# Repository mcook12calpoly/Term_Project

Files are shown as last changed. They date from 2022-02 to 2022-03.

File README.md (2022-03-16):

# Term Project - Plotting Machine

For this term project, a 2.5 axis plotting machine was contructed using a pivoting arm driven by a motor attached to a wheel at the end of the arm. Alongside the arm, a lead screw driven by a second motor which will move a pen carrier linearly along the arm. Within the pen carrier is a servo attached to the pen to raise and lower the pen. A small piece wraps around tip of the pen to allow the servo arm to push it upwards. The body of the arm and the base is made of square metal tubing and the pen chassis as well as the coupling piece that connects the arm and carrier to keep the pen carrier upright will be 3D printed. The pivoting mechanism includes a bearing to minimize slop in our rotation. Limit switches are used to signal when the arm is in its home position. The encoders included with the motors are used to track the movement of the arm and determine the pen's location. The code uses kinematic calculations to convert the x,y plot directions to the curvilinear movement of the arm and pen carrier.

---

### Bill of Materials

| Qty. | Part | Source | Est. Cost |
|:----:|:---|:---|:---:|
|  2 | Pittman Gearmotors | ME405 Tub | - |
|  1 | Nucleo with Shoe | ME405 Tub | - |
|  1 | Nucleo Motor Driver | ME405 Tub | - |
|  5 | Hobby Micro Servo | Amazon&trade; | $8.99 |
|  1 | 400mm Lead Screw | Amazon&trade; | $12.99  |
|  1 | 96" Square Metal Tube | Home Depot&trade; | $22.26  |
|  1 | Triplus Fineliner Pen | Already Owned | $1.29 |
|  1 | Chassis for servo/pen | 3D Printer | - |
|  1 | Limit Switch | Already Owned | - |
|  2 | Wheel | 3D Printer | - |

---
### Hardware Design
The frame for our machine was constructed of aluminum tubing and 3d printed connectors. The central connector had mounting points for the pivot arm's limit switch as well as the hinge for the pivot arm. The pivot arm was also constructed out of alumininum tubing with a 3d printed motor mount and coupler at the end that attached to a 3d printed wheel with rubber bands for grip. Opposite the wheel on the arm is another 3d printed motor mount and coupler that operated the lead screw which is supported by a bearing on the other end placed within the wheel motor's mount. The pen holder was also 3d printed and made to wrap around the pivot arm and move with the lead screw by attaching to the copper nut provided with the lead screw. 

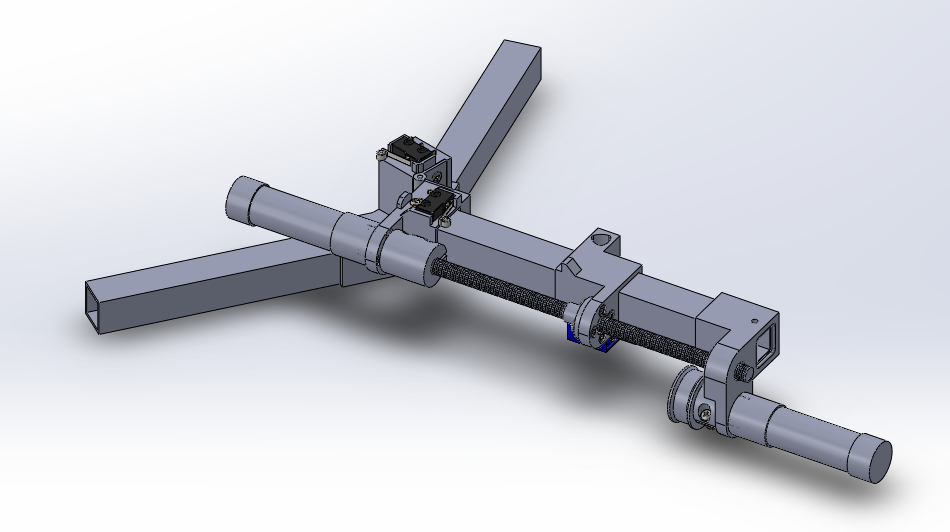
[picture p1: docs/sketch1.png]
projectsketch1

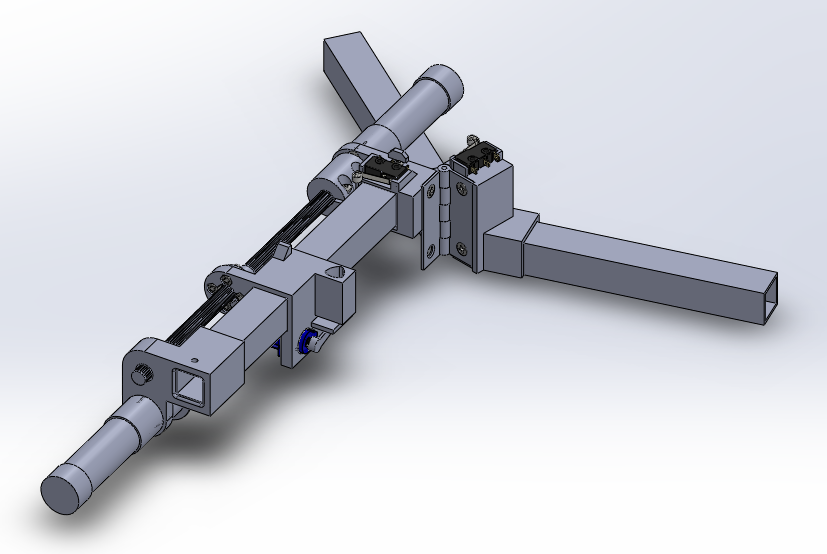
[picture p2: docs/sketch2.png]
projectsketch2

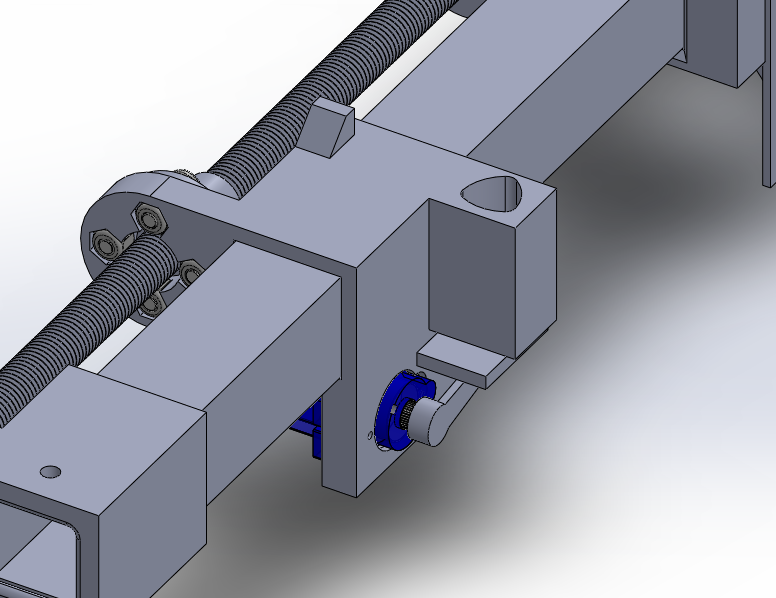
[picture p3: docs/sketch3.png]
projectsketch3


---
### Software Design
The software begins with a custom GCode file that is processed through a script that goes line by line and convcerts each command into polar setpoints of r and theta and a pen state(up or down). This processed list of setpoints is then loaded on the board where it can be read by the main file, with each line placed in a queue. After initially sending both motors (screw and wheel) back to their home positions near the origin, three tasks are created and added to the task list: update encoder, move and read. The update encoder task updates the encoder drivers to get the current position values for both motors, the move task moves the motors (and pen servo if applicable) until their corresponding enocders reach the current setpoint on the top of the queue. The read task adds each line of setpoints to the queue one at a time.

Link to Doxygen: https://mcook12calpoly.github.io/Term_Project/

---
### Results
After some initial testing and reworking of our software, the first successful drawing was of a rectangle. Due to the changes made on how the Gcode processing script determines the resolution of each line drawn, we were able to get much better looking and consistent long lines. The lines of the rectangle did not display any large zigzags as our device had been producing before the changes. However, the lines were not perfectly aligned and created angles that were not 90 degrees in the rectangle. We believe that this issue was due to the home position of our pen holder relative to the expected origin of our axis.

---
### Lessons Learned
The combination of 3d printed parts and aluminum tubing for the frame of the machine made the construction very durable for our testing uses and allowed the mechanical side of the machine to run without issue, leaving more time to focus on software.

We did not initially think to factor in the distance between the pivot(hinge) and the resting home position of the pen in its holder. This would have given us an offset radial value for what should be home or (0,0). This is likely why our rectange did not have straight angles in our testing. In addition, we learned quite a bit about task timing and efficiency. Reducing the period of certain tasks such as our move task and read task greatly improved the resolution of our machine, as it took less time for the next setpoint to be ready. 

If we were to write the code for this machine again, one improvement that we would make would be to implement Bresenham's line drawing algorithm, which would better help us calculate setpoints so that the steps in straight lines are less noticable. In addition to this, we would parse the setpoints and load them into memory before the machine runs, instead of parsing the setpoints each time the read task is called. This would likely improve the performance of our program, allowing us to run at finer setpoint resolutions. Although we didn't experience any issues with sensor resolution, their effect(especially on the wheel) could be noticable with better code performance. A potentiometer could be implemented on the pivot of the arms, which would allow for better accuracy and negate any error from wheel slippage. Also, the implementation of a PID controller could help with line smoothness due to the acceleration and decelleration of both axis.

---

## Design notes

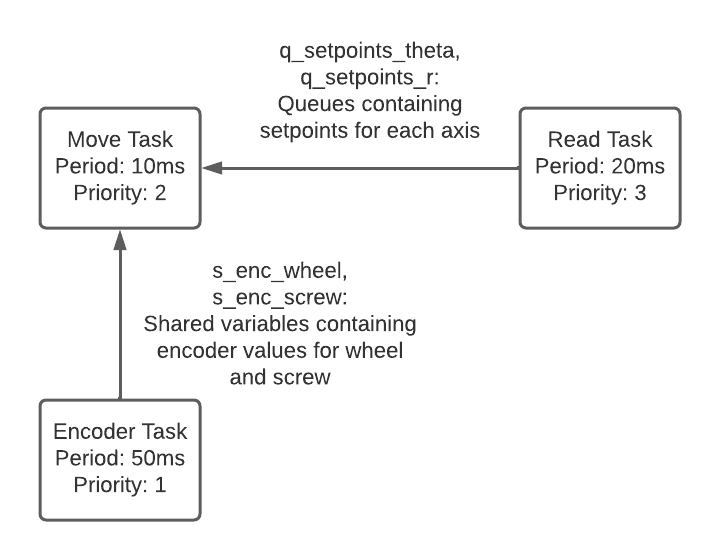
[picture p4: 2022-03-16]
docs/Task_Diagram.png

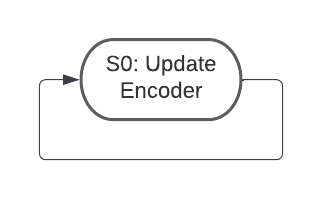
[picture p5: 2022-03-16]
docs/Encoder_FSM.png

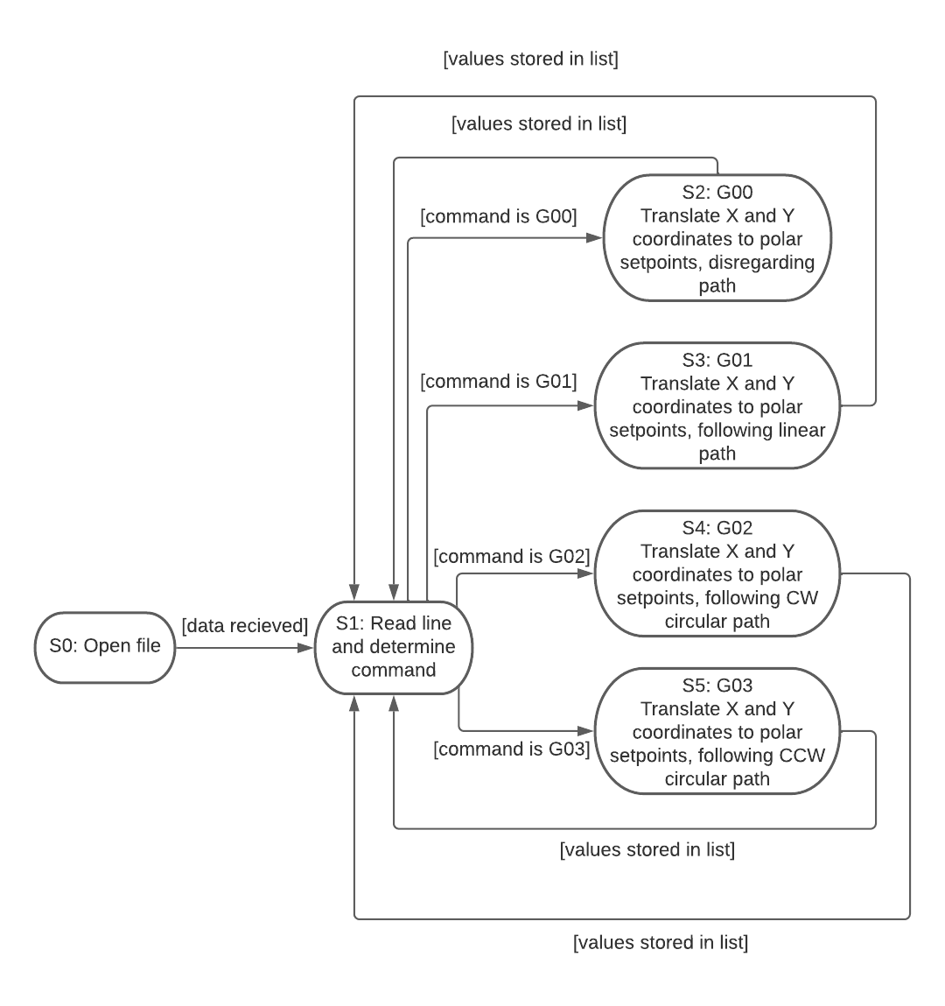
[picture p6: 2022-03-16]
docs/G_Code_FSM.png

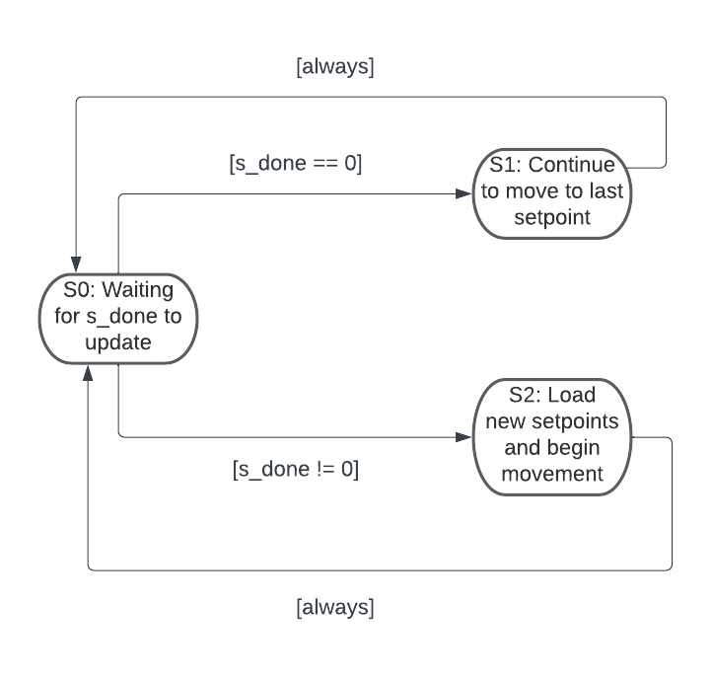
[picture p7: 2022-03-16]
docs/Main_FSM.png

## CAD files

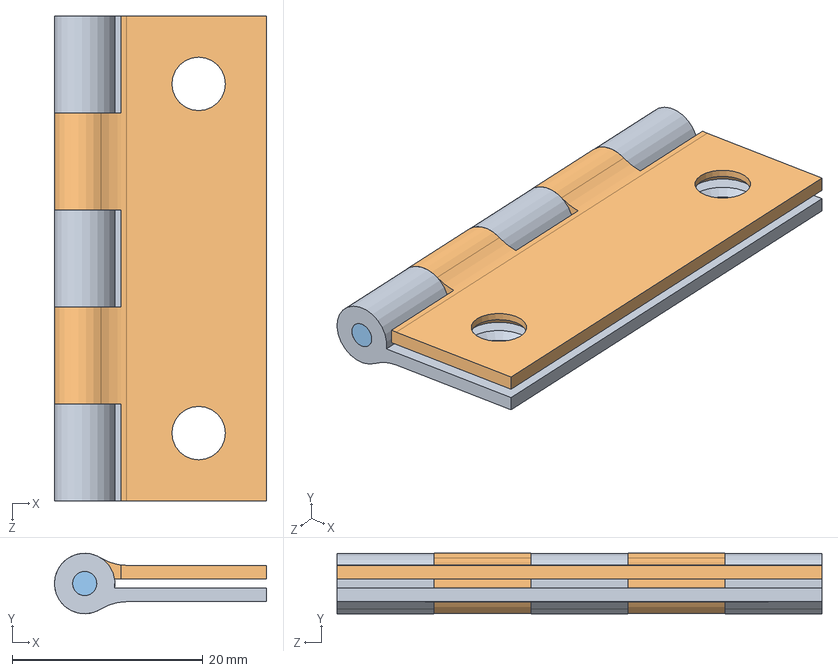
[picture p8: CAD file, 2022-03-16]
CAD/HINGE_ASSEMBLY.SLDASM
22.2 x 6.34 x 50.8 mm
HINGE_1
HINGE_2
HINGE_PIN

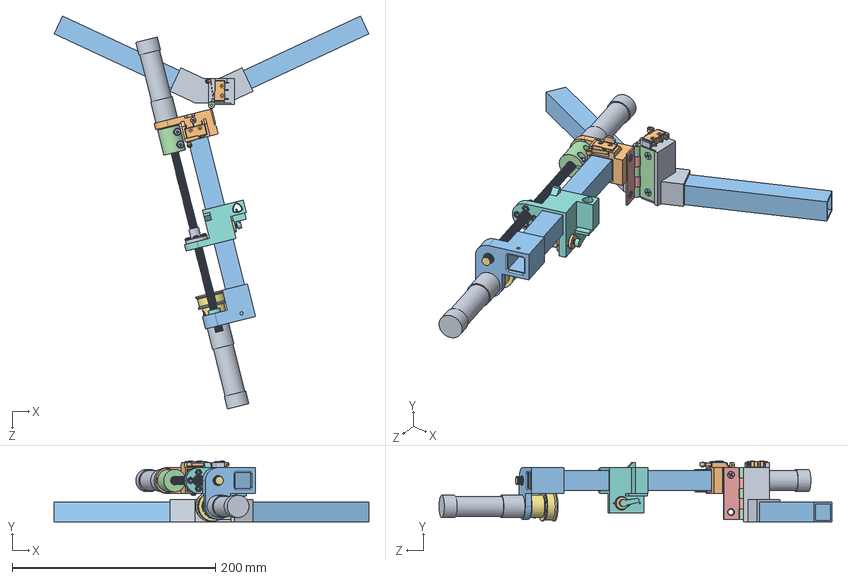
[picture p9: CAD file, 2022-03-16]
CAD/PLOTTER_ASSEMBLY.SLDASM
309.3 x 59.7 x 386.3 mm
MIDDLE_BRACKET
ARM_BRACKET
WHEEL_BRACKET
COUPLER
93625A100_18-8 Stainless Steel Nylon-Insert Locknut x 7
90116A155_316 Stainless Steel Pan Head Phillips Screws x 15
WHEEL
SLIDER
LEADSCREW_NUT
MICRO SERVO
ALUMINUM_TUBE x 3
HINGE_1
HINGE_2
HINGE_PIN
LEADSCREW
BEARING
MOTOR x 2
MICROSWITCH x 2
90031A151_Phillips Flat Head Screws for Wood x 2
90101A007_18-8 Stainless Steel Thin Nylon-Insert Locknut
91771A148_Passivated 18-8 Stainless Steel Phillips Flat Head Screw
91772A108_Passivated 18-8 Stainless Steel Pan Head Phillips Screw x 2
90633A005_Low-Strength Steel Thin Nylon-Insert Locknut x 2
SERVO HORN

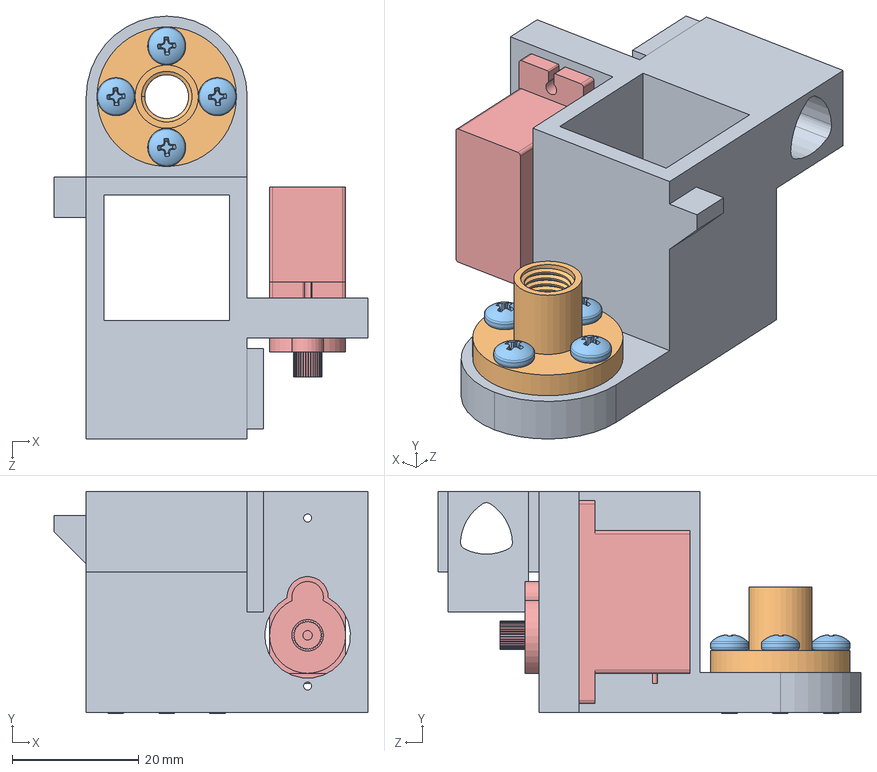
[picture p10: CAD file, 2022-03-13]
CAD/SLIDER_ASSEMBLY.SLDASM
49.5 x 35.1 x 66.7 mm
SLIDER
LEADSCREW_NUT
90116A155_316 Stainless Steel Pan Head Phillips Screws x 4
93625A100_18-8 Stainless Steel Nylon-Insert Locknut x 4
MICRO SERVO

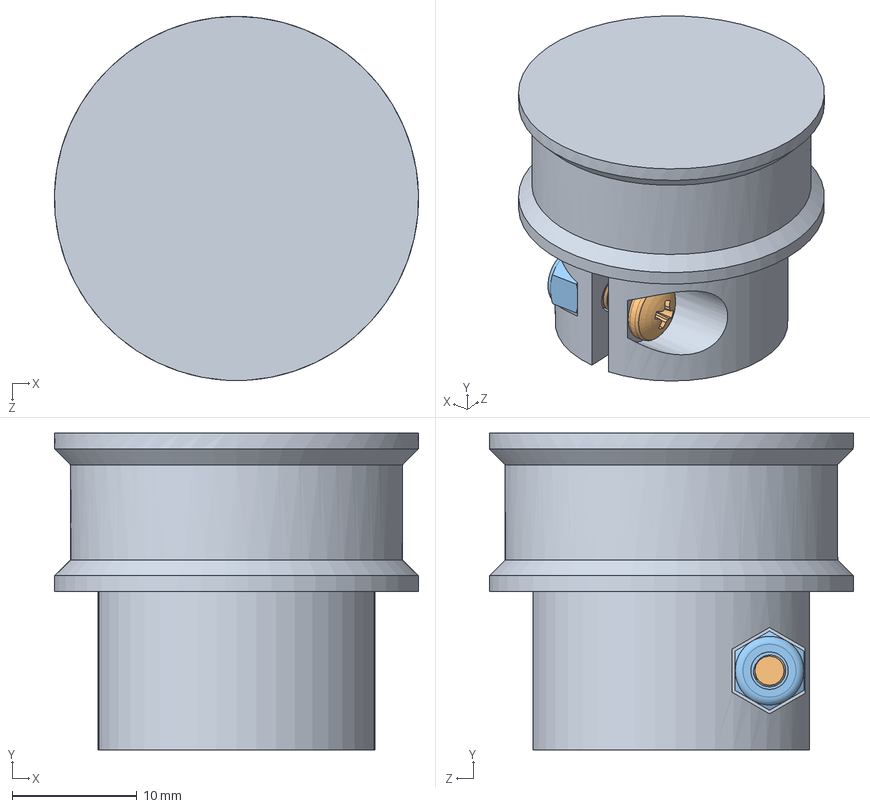
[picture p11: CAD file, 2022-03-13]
CAD/WHEEL_ASSEMBLY.SLDASM
29.2 x 25.4 x 29.2 mm
WHEEL
90116A155_316 Stainless Steel Pan Head Phillips Screws
93625A100_18-8 Stainless Steel Nylon-Insert Locknut

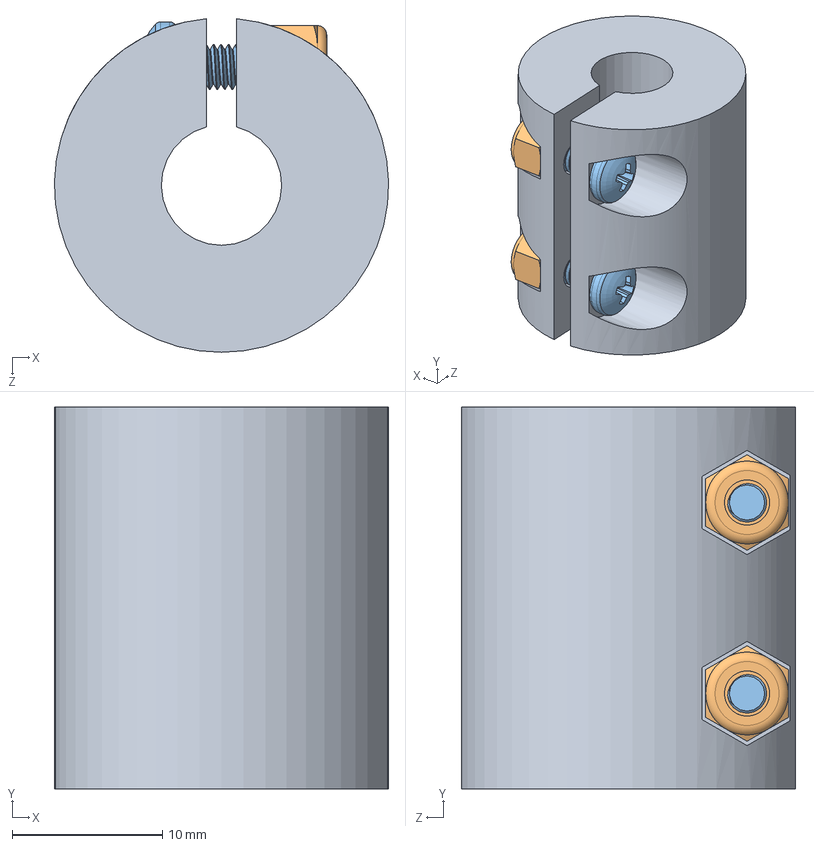
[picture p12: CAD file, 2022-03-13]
CAD/COUPLER_ASSEMBLY.SLDASM
22.2 x 25.4 x 22.2 mm
COUPLER
93625A100_18-8 Stainless Steel Nylon-Insert Locknut x 2
90116A155_316 Stainless Steel Pan Head Phillips Screws x 2

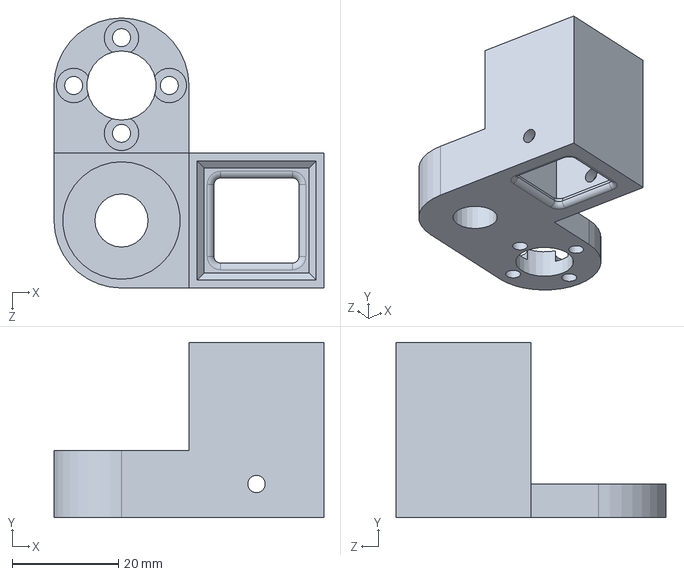
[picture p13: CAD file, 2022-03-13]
CAD/WHEEL_BRACKET.SLDPRT
50.8 x 33.0 x 50.8 mm

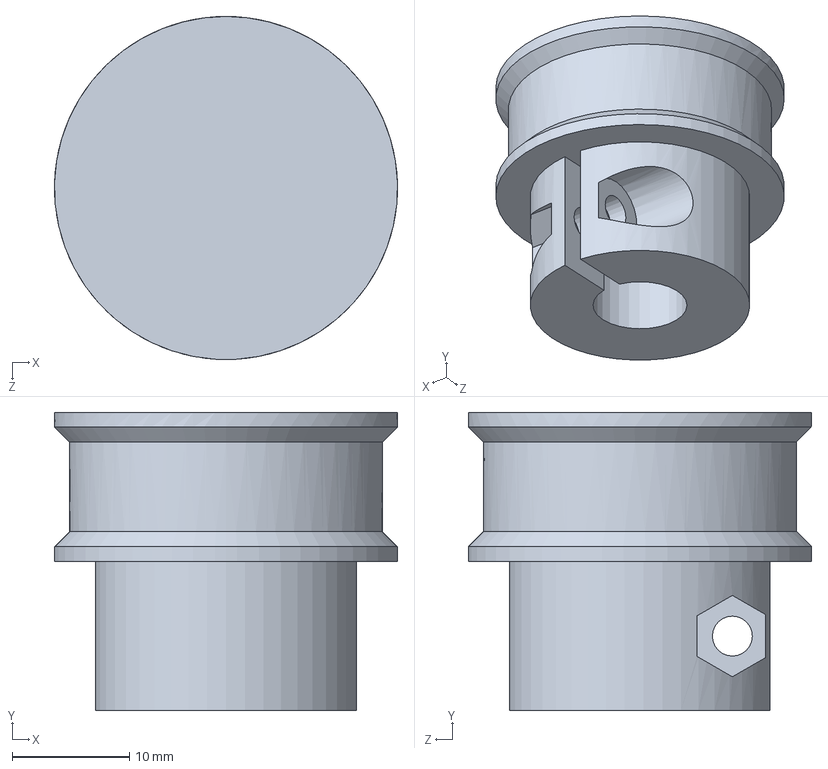
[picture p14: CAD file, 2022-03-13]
CAD/WHEEL.SLDPRT
29.2 x 25.4 x 29.2 mm

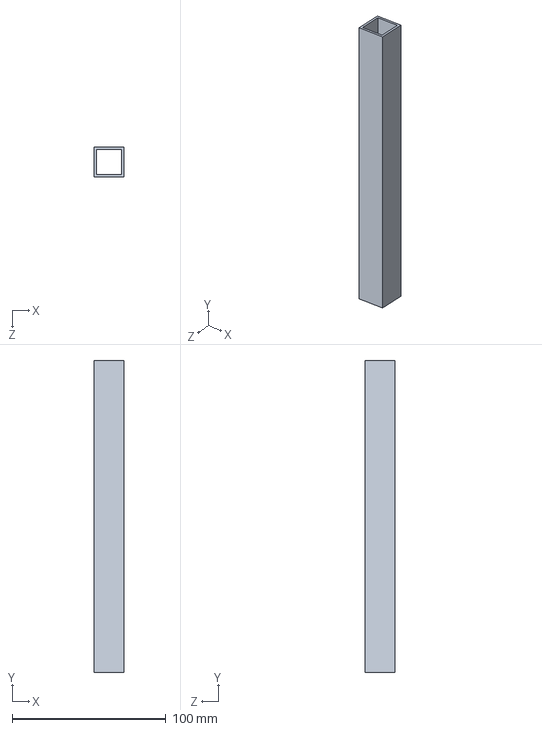
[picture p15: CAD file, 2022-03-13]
CAD/ALUMINUM_TUBE.SLDPRT
19.3 x 203.2 x 19.3 mm

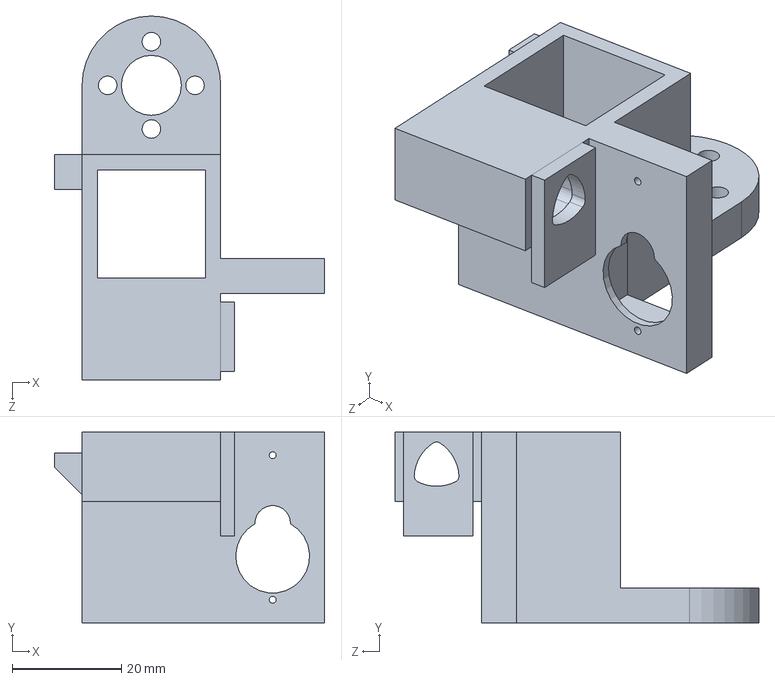
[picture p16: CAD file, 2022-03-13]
CAD/SLIDER.SLDPRT
49.5 x 34.9 x 66.7 mm

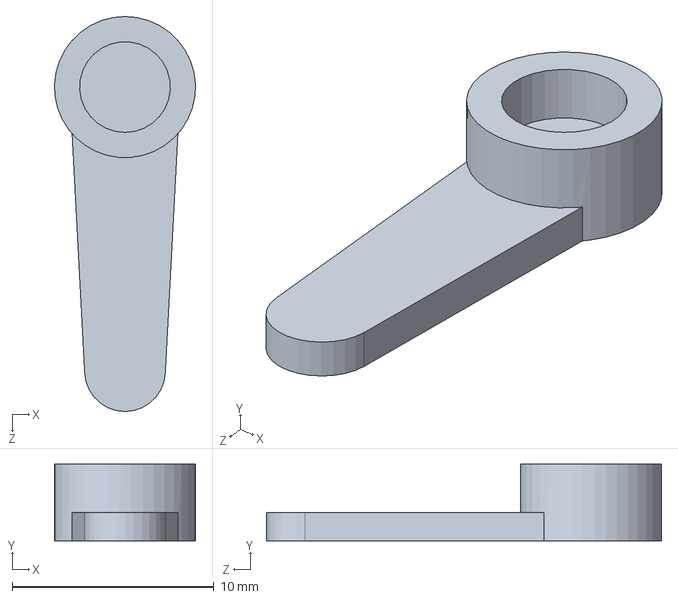
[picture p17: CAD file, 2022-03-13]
CAD/SERVO HORN.SLDPRT
6.99 x 3.80 x 19.6 mm

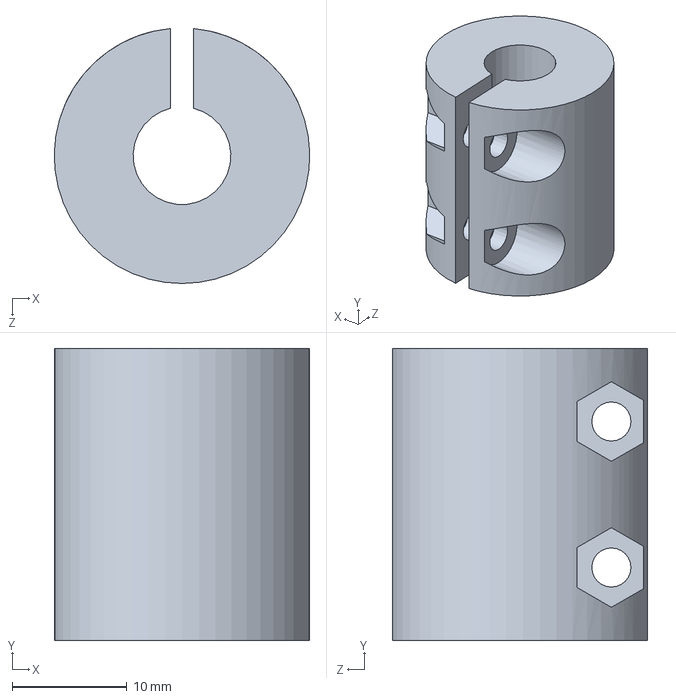
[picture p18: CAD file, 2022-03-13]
CAD/COUPLER.SLDPRT
22.2 x 25.4 x 22.2 mm

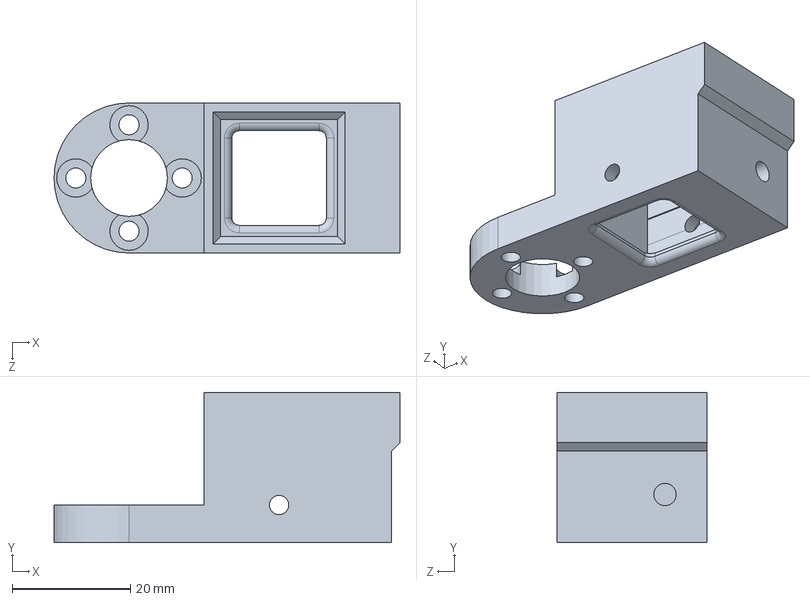
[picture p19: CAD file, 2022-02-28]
CAD/ARM_BRACKET.SLDPRT
58.6 x 25.4 x 25.4 mm

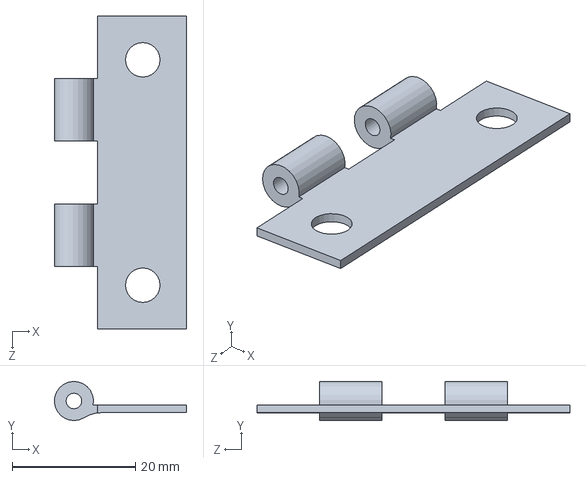
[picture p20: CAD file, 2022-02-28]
CAD/HINGE_2.SLDPRT
21.5 x 6.34 x 50.8 mm

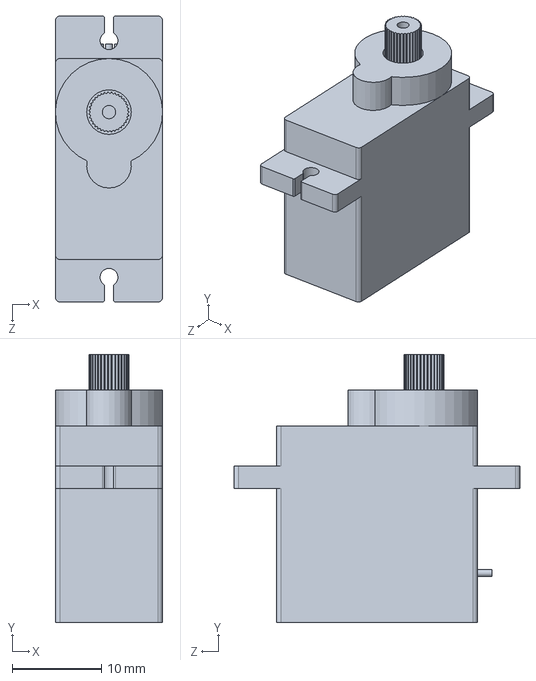
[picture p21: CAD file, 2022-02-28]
CAD/MICRO SERVO.SLDPRT
12.0 x 30.0 x 32.0 mm

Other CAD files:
CAD/HINGE_1.SLDPRT
CAD/MIDDLE_BRACKET.SLDPRT
CAD/MOTOR.SLDPRT
CAD/BEARING.SLDPRT
CAD/90031A151_Phillips Flat Head Screws for Wood.SLDPRT
CAD/90101A007_18-8 Stainless Steel Thin Nylon-Insert Locknut.SLDPRT
CAD/90116A155_316 Stainless Steel Pan Head Phillips Screws.SLDPRT
CAD/90633A005_Low-Strength Steel Thin Nylon-Insert Locknut.SLDPRT
CAD/91771A148_Passivated 18-8 Stainless Steel Phillips Flat Head Screw.SLDPRT
CAD/91772A108_Passivated 18-8 Stainless Steel Pan Head Phillips Screw.SLDPRT
CAD/91772A194_Passivated 18-8 Stainless Steel Pan Head Phillips Screw.SLDPRT
CAD/91841A007_18-8 Stainless Steel Hex Nut.SLDPRT
CAD/93625A100_18-8 Stainless Steel Nylon-Insert Locknut.SLDPRT
CAD/HINGE_PIN.SLDPRT
CAD/LEADSCREW.SLDPRT
CAD/LEADSCREW_NUT.SLDPRT
CAD/MICROSWITCH.SLDPRT
CAD/STL/ARM_BRACKET.STL
CAD/STL/COUPLER.STL
CAD/STL/MIDDLE_BRACKET.STL
CAD/STL/WHEEL.STL
CAD/STL/WHEEL_BRACKET.STL

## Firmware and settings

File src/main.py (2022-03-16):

'''! @file      main.py
                This program is the main program for controlling our 2.5 axis pen plotter.
                It utilizes cooperative multi tasking, with 3 main tasks- updating the encoder, moving the motors, and parsing/storing setpoint values.
    @author     Michael Cook
    @author     Derick Louie
    @date       March 14, 2022
    @copyright  (c) 2022 by Michael Cook, Derick Louie, and released under GNU Public License v3
'''

import gc
import pyb
import cotask
import task_share
import time
from switch import Switch
from encoder import Encoder
from motordriver import MotorDriver
from home import Home
from controller import Controller
from pen import Pen

def task_encoder_update():
    """!
    Task which reads and stores encoder values into shared variables
    """
    while True:
        enc_wheel.update()
        enc_screw.update()
        
        s_enc_wheel.put(-enc_wheel.read())    
        s_enc_screw.put(enc_screw.read())

        #print("Wheel:", s_enc_wheel.get(), "Screw:", s_enc_screw.get())
        yield(0)
        
def task_move():
    """!
    Task which moves the motors using the functions in controller.py
    """
    setpoint_theta = 0
    setpoint_r = 0
    setpoint_pen = 0
    
    while True:
        #print("Theta setpoint:", setpoint_theta, "R setpoint:", setpoint_r, "Pen setpoint:", setpoint_pen)
        #print("done flag:", s_done.get())
        
        if s_done.get() == 0:
            
            # target theta, theta speed, target r, r speed, theta threshold, r threshold
            controller.moveto(setpoint_theta, 50, setpoint_r, 75, setpoint_pen)
        
        else:
            if q_setpoints_theta.any():
                setpoint_theta = q_setpoints_theta.get()
                setpoint_r = q_setpoints_r.get()
                setpoint_pen = q_setpoints_pen.get()
                s_done.put(0)
                
            else:
                controller.moveto(setpoint_theta, 50, setpoint_r, 75, setpoint_pen)

        yield(0)
        
def task_read():
    """!
    Task which parses and stores setpoints in queue
    """
    values_split = []
    file = open('setpoints.txt', 'r')
    values = file.read()
    file.close()
    values = values.replace('[','')
    values = values.replace(']','')
    values = values.replace(' ','')
    
    values = values.splitlines()
    
    for i in values:
        values_split.append(i.rsplit(','))
    
    #print(values_split)
    
    while True:
        #gc.collect()
        if not q_setpoints_theta.full():
            
            if values_split:
                q_setpoints_theta.put(float(values_split[0][1]))
                q_setpoints_r.put(float(values_split[0][0]))
                q_setpoints_pen.put(int(values_split[0][2]))
                values_split.pop(0)
            
        yield(0)
        
if __name__ == "__main__":
    
    
    # creating shares
    s_enc_screw = task_share.Share ('i', thread_protect = False, name = "screw encoder")
    
    s_enc_wheel = task_share.Share ('i', thread_protect = False, name = "wheel encoder")
    
    s_done = task_share.Share ('i', thread_protect = False, name = "done flag")
    
    q_setpoints_theta = task_share.Queue ('f', 50, thread_protect = False, overwrite = False, name = "theta setpoints")
    
    q_setpoints_r = task_share.Queue ('f', 50, thread_protect = False, overwrite = False, name = "r setpoints")
    
    q_setpoints_pen = task_share.Queue ('i', 50, thread_protect = False, overwrite = False, name = "pen setpoints")
    
    # initial points in case queue empty
    q_setpoints_theta.put(0)
    q_setpoints_r.put(0)
    q_setpoints_pen.put(0)
    
    # creating encoder objects
    enc_wheel = Encoder(pyb.Pin.board.PB6, pyb.Pin.board.PB7, 4)
    enc_screw = Encoder(pyb.Pin.board.PC6, pyb.Pin.board.PC7, 8)
    
    # creating motor objects
    motor_wheel = MotorDriver(pyb.Pin.board.PA10, pyb.Pin.board.PB4, pyb.Pin.board.PB5, 3)
    motor_screw = MotorDriver(pyb.Pin.board.PC1, pyb.Pin.board.PA0, pyb.Pin.board.PA1, 5)
    
    # creating switch objects
    switch_wheel = Switch(pyb.Pin.board.PB8)
    switch_screw = Switch(pyb.Pin.board.PC2)
    
    # creating pen object
    pen = Pen()
    
    # move pen up at start
    pen.up()
    
    # creating controller object
    controller = Controller(motor_wheel, s_enc_wheel, motor_screw, s_enc_screw, pen, s_done)
    
    
    home = Home()
    home.goHome(motor_screw, enc_screw, switch_screw, 0, 75)
    home.goHome(motor_wheel, enc_wheel, switch_wheel, 1, 50)
    
    del enc_screw
    del enc_wheel
    
    time.sleep_ms(500)
    
    enc_wheel = Encoder(pyb.Pin.board.PB6, pyb.Pin.board.PB7, 4)
    enc_screw = Encoder(pyb.Pin.board.PC6, pyb.Pin.board.PC7, 8)


    #q0 = task_share.Queue ('L', 16, thread_protect = False, overwrite = False,
    #                       name = "Queue 0")

    task1 = cotask.Task (task_encoder_update, name = 'update encoder', priority = 1, 
                         period = 50, profile = True, trace = False)

    task2 = cotask.Task (task_move, name = 'move', priority = 2, 
                         period = 10, profile = True, trace = False)
    
    task3 = cotask.Task (task_read, name = 'serial read', priority = 3, 
                         period = 20, profile = True, trace = False)
    
    cotask.task_list.append (task1)
    cotask.task_list.append (task2)
    cotask.task_list.append (task3)

    gc.collect ()

    while (True):
        cotask.task_list.pri_sched ()
        

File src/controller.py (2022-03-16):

'''! @file      controller.py
                This program includes functions for the motor controller, moving the machine to setpoints.
    @author     Michael Cook
    @author     Derick Louie
    @date       March 15, 2022
    @copyright  (c) 2022 by Michael Cook, Derick Louie, and released under GNU Public License v3
'''

class Controller:
    
    def __init__ (self, motor_theta, encoder_theta, motor_r, encoder_r, pen, done_flag):
        '''! 
        Initializes variables and passes motors, encoders, servo, and shared variable in.
        @param motor_theta Motor that controls theta axis
        @param encoder_theta Encoder for theta axis
        @param motor_r Motor that controls r axis
        @param encoder_r Encoder for r axis
        @param pen Pen object
        @param done_flag Shared variable indicating if last setpoint has been reached
        '''        
        self.motor_theta = motor_theta
        self.encoder_theta = encoder_theta
        
        self.motor_r = motor_r
        self.encoder_r = encoder_r
        
        self.done_flag = done_flag
        
        self.pen = pen
        
    def moveto (self, target_theta, speed_theta, target_r, speed_r, target_pen, theta_threshold = 350, r_threshold = 500):
        '''! 
        Moves motors to setpoint with a certain speed and threshold
        @param target_theta Theta axis setpoint
        @param speed_theta Theta axis speed
        @param target_r r axis setpoint
        @param speed_r r axis speed
        @param target_pen Pen setpoint
        @param theta_threshold Acceptable threshold(error) from setpoint for theta axis
        @param r_threshold Acceptable threshold(error) from setpoint for r axis
        
        '''        
        # thresholds in ticks
        # 4.3125 inches = 112000 ticks
        # 180 degrees = 44000 ticks
        
        target_theta = target_theta * 44000 / 180
        target_r = target_r * 112000 / 4.3125
        
        if (abs(target_theta - self.encoder_theta.get()) < theta_threshold):
            self.motor_theta.set_duty_cycle(0)
            self.done_flag.put(1)
            #print("WITHIN THRESHOLD")
            
        elif (self.encoder_theta.get() > target_theta):
            self.motor_theta.set_duty_cycle(speed_theta)
            #print("still good", self.encoder_r.get())
            
        elif (self.encoder_theta.get() < target_theta):
            self.motor_theta.set_duty_cycle(-speed_theta)
    
        if (abs(target_r - self.encoder_r.get()) < r_threshold):
            self.motor_r.set_duty_cycle(0)
            self.done_flag.put(1)
            #print("WITHIN THRESHOLD")
            
        elif (self.encoder_r.get() > target_r):
            self.motor_r.set_duty_cycle(speed_r)
            #print("still good", self.encoder_r.get())
            
        elif (self.encoder_r.get() < target_r):
            self.motor_r.set_duty_cycle(-speed_r)
            
        if target_pen == 1:
            self.pen.down()
            
        elif target_pen == 0:
            self.pen.up()
            

        
if __name__ == "__main__":

    enc_wheel = Encoder(pyb.Pin.board.PB6, pyb.Pin.board.PB7, 4)
    enc_screw = Encoder(pyb.Pin.board.PC6, pyb.Pin.board.PC7, 8)
    
    motor_wheel = MotorDriver(pyb.Pin.board.PA10, pyb.Pin.board.PB4, pyb.Pin.board.PB5, 3)
    motor_screw = MotorDriver(pyb.Pin.board.PC1, pyb.Pin.board.PA0, pyb.Pin.board.PA1, 5)
    
    

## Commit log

2022-02-22 Create Encoder FSM.png
2022-02-22 Update Encoder FSM.png
2022-02-28 CAD files
    [90031A151_Phillips Flat Head Screws for Wood.SLDPRT, 90101A007_18-8 Stainless Steel Thin Nylon-Insert Locknut.SLDPRT, 90116A155_316 Stainless Steel Pan Head Ph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]
2022-03-01 rename servodriver
2022-03-06 add motordriver, encoder
2022-03-08 update gcodereader
    [gcode.csv]
2022-03-13 final cad models
    [ALUMINUM_TUBE.SLDPRT, ARM_BRACKET.STL, COUPLER.SLDPRT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]
